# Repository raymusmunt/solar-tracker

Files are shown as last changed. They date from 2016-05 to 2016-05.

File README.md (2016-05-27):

# Solar Tracker
A solar tracking system using a barndoor mechanism with a Arduino microcontroller

**All 3D printable items can be found in the sketchup document**
- Brain Housing
- Motor housing hinge
- Captive bolt hinge
- Omron switch endstops
- LDR mount

Frame made with wood, attached to satellite mount with pole clamps.
Adjustable Solar Panel fixture made from aluminium cornering.

Worm gearing made with m10 threaded rod and nuts.
Motor Hinge and Captive bolt hinge also using threaded rod and bolts.

**Electronics**
- x2 LDR
- x2 Weatherproof microswitches
- x4 10K Resistors
- LM293B
- x4 Diodes (not needed if using LM293D)
- 12V DC Motor

Big thanks to all the folks at #Arduino for the help and encouragement!

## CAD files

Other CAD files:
assembly/solar_tracker_sketchup.skp

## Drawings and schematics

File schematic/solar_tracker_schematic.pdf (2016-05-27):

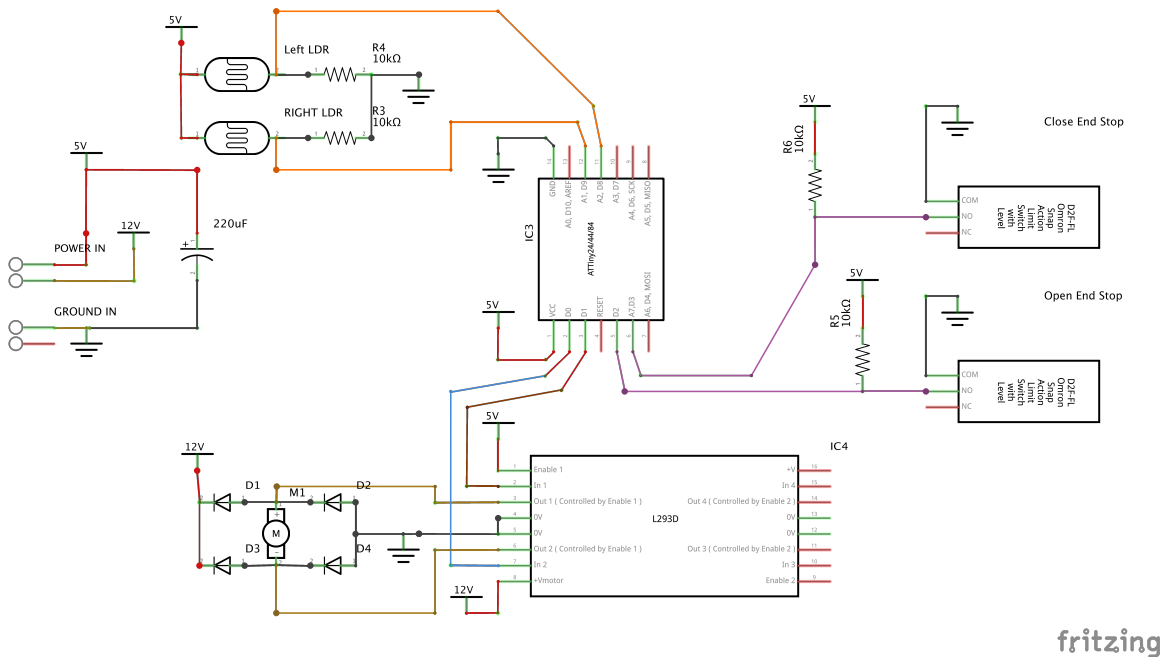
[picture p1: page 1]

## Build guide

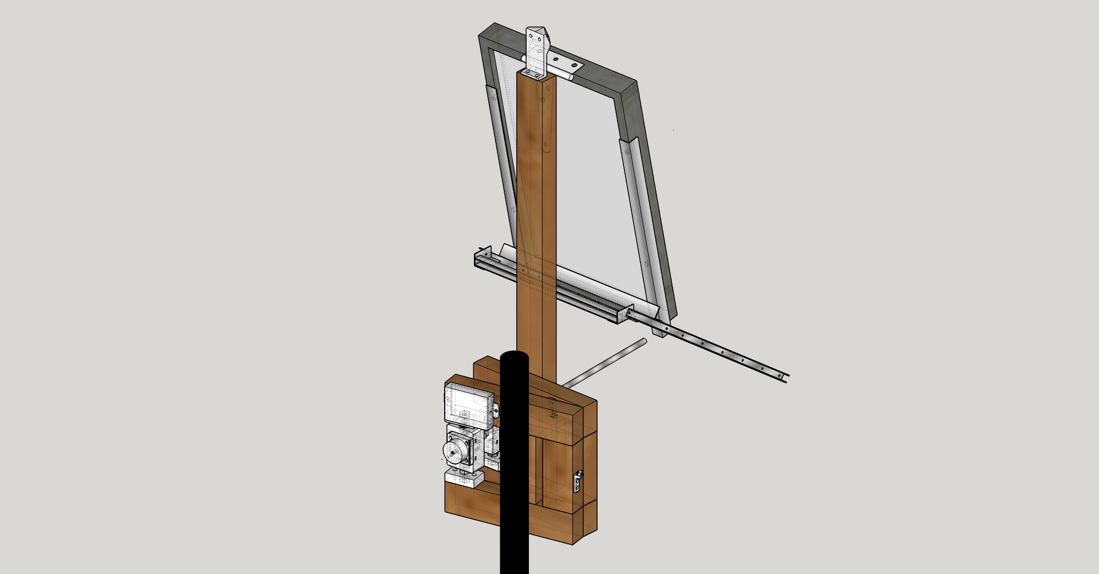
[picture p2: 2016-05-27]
assembly/solar_tracker_sketchup_back.jpg

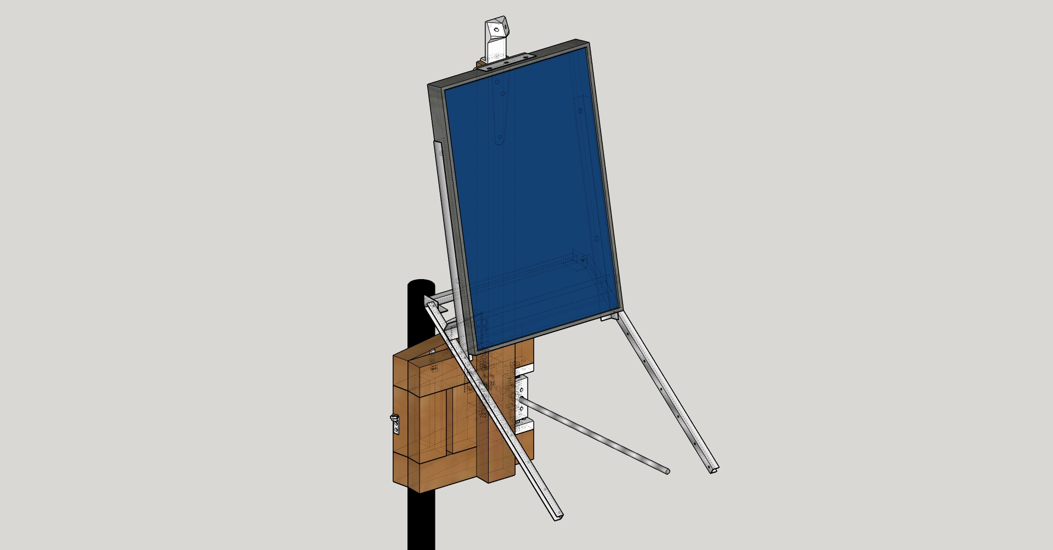
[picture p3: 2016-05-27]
assembly/solar_tracker_sketchup_front.jpg

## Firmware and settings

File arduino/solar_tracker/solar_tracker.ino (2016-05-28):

// ATMEL ATTINY84 / ARDUINO
//
//                           +-\/-+
//                     VCC  1|    |14  GND
//             (D 10)  PB0  2|    |13  AREF (D  0)
//             (D  9)  PB1  3|    |12  PA1  (D  1)
//                     PB3  4|    |11  PA2  (D  2)
//  PWM  INT0  (D  8)  PB2  5|    |10  PA3  (D  3)
//  PWM        (D  7)  PA7  6|    |9   PA4  (D  4)
//  PWM        (D  6)  PA6  7|    |8   PA5  (D  5)        PWM
//                           +----+

//////////////////
// SERIAL DEBUG //
//////////////////

// uncomment '#define DEBUG' to enable serial debug
//#define DEBUG

#ifdef DEBUG
  #include <SoftwareSerial.h>
  SoftwareSerial mySerial(4, 5);
  
  #define DEBUG_BEGIN(x) mySerial.begin(x)
  #define DEBUG_PRINT(x)     mySerial.print (x)
  #define DEBUG_PRINTLN(x)  mySerial.println (x)
  #define DEBUG_DELAY(x) delay(x)
  #else
  #define DEBUG_BEGIN(x)
  #define DEBUG_PRINT(x)
  #define DEBUG_PRINTLN(x)
  #define DEBUG_DELAY(x)
#endif

////////////////////
// WATCHDOG RESET //
////////////////////

#include <avr/sleep.h>
#include <avr/wdt.h>

ISR(WDT_vect)
{
  wdt_disable();  // disable watchdog
}

//////////////////////
// GLOBAL VARIABLES //
//////////////////////

#define LDR_LEFT A2
#define LDR_RIGHT A1

#define MOTOR_OPEN 10
#define MOTOR_CLOSE 9

#define SWITCH_OPEN 8
#define SWITCH_CLOSE 7

#define LEFT_FUDGE 0.015 // LeftSensor adjustment e.g. '0.11' adds 11%
#define TOTAL_FUDGE 2 // Add some slop to the motor centered figure.

#define NIGHT_VALUE 720

#define SLEEP_TIME 15 // 15 = 2min (8s * 15)

enum State {
  MAIN,
  GO_HOME,
  TRACK,
  SLEEP
};

State currentState = MAIN;

int ldrLeft, ldrRight;

////////////
// SETUP  //
////////////

void setup() {

  DEBUG_BEGIN(9600);

  pinMode(LDR_LEFT, INPUT);
  pinMode(LDR_RIGHT, INPUT);

  pinMode(MOTOR_OPEN, OUTPUT);
  pinMode(MOTOR_CLOSE, OUTPUT);

  pinMode(SWITCH_OPEN, INPUT);
  pinMode(SWITCH_CLOSE, INPUT);
}

///////////////
// MAIN LOOP //
///////////////

void loop() {

  DEBUG_DELAY(1000);

  switch ( currentState ) {

    /**
       [MAIN]
        Determines which state to enter based on ambient light
    */
    case MAIN:
      DEBUG_PRINTLN("State: MAIN");

      if ( isDaytime() ) {
        currentState = TRACK;
      } else if ( !isDaytime() ) {
        currentState = GO_HOME;
      }
      break;

    /**
       [TRACK]
        Looks for the sun and controls the motor allowing TOTAL_FUDGE slack
        in readings. Stops motor on contact with corresponding end stop.
    */
    case TRACK:
      DEBUG_PRINTLN("State: TRACK");

      readLDRs();

      if (ldrRight >= ldrLeft - TOTAL_FUDGE && ldrRight <= ldrLeft + TOTAL_FUDGE) {
        DEBUG_PRINTLN("Sweet Spot");
        stopMotor();
        currentState = MAIN;
        break;
      }
      
      if ( ldrRight > ldrLeft) {
        if ( !digitalRead(SWITCH_OPEN) ) {
          DEBUG_PRINTLN("Open End Stop");
          stopMotor();
          currentState = MAIN;
          break;
        }
        goRight();
      }
      
      else if ( ldrRight < ldrLeft ) {
        if ( !digitalRead(SWITCH_CLOSE) ) {
          DEBUG_PRINTLN("Closed End Stop");
          stopMotor();
          currentState = MAIN;
          break;
        }
        goLeft();
      }

      currentState = MAIN;
      break;

    /**
       [GO_HOME]
        Returns the panel to western configuration until
        it hits the end stop and goes to sleep.
    */
    case GO_HOME:
      DEBUG_PRINTLN("State: GO_HOME");
      if (!digitalRead(SWITCH_CLOSE)) {
        stopMotor();
        currentState = SLEEP;
        break;
      }
      goLeft();
      currentState = MAIN;
      break;

    /**
       [SLEEP]
        Power down for 8 seconds * SLEEP_TIME.
        http://forum.arduino.cc/index.php?topic=173850.msg1291338#msg1291338
    */
    case SLEEP:
      DEBUG_PRINTLN("State: SLEEP");

      for ( int i = 0; i < SLEEP_TIME; i++ ) {
        MCUSR = 0;                          // reset various flags
        WDTCSR |= 0b00011000;               // see docs, set WDCE, WDE
        WDTCSR =  0b01000000 | 0b100001;    // set WDIE, and 8s delay

        wdt_reset();
        set_sleep_mode (SLEEP_MODE_PWR_DOWN);
        sleep_mode();            // now goes to Sleep and waits for the interrupt
      }

      DEBUG_PRINTLN("Waking!");
      currentState = MAIN;
      break;

    default:
      DEBUG_PRINTLN("CODE FAILURE");
      stopMotor();
      currentState = MAIN;
      break;
  }
}

///////////////
// UTILITIES //
///////////////

void readLDRs () {
  ldrLeft = analogRead(LDR_LEFT);
  ldrRight = analogRead(LDR_RIGHT);

  DEBUG_PRINT("LDR L : ");
  DEBUG_PRINT(ldrLeft);

  float ldrLeftFudge = ldrLeft * LEFT_FUDGE;  // Calculate LEFT_FUDGE%
  ldrLeft = ldrLeft + (int)ldrLeftFudge;

  DEBUG_PRINT(" LDR L FUDGED : ");
  DEBUG_PRINT(ldrLeft);
  DEBUG_PRINT(" FUDGEVAL: ");
  DEBUG_PRINT(ldrLeftFudge);
  DEBUG_PRINT(" LDR R: ");
  DEBUG_PRINTLN(ldrRight);
}

bool isDaytime()
{
  readLDRs();

  if ( ldrLeft > NIGHT_VALUE || ldrRight > NIGHT_VALUE ) {
    return true;
  }
  return false;
}

////////////////////
// MOTOR CONTROLS //
////////////////////

void goRight()
{
  DEBUG_PRINTLN("Going Right");
  digitalWrite(MOTOR_OPEN, HIGH);
  digitalWrite(MOTOR_CLOSE, LOW);
}

void goLeft()
{
  DEBUG_PRINTLN("Going Left");
  digitalWrite(MOTOR_OPEN, LOW);
  digitalWrite(MOTOR_CLOSE, HIGH);
}

void stopMotor()
{
  DEBUG_PRINTLN("Stopping");
  digitalWrite(MOTOR_OPEN, LOW);
  digitalWrite(MOTOR_CLOSE, LOW);
}

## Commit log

2016-05-27 First Commit
    This appears to be working :) Any questions feel free to ask.
    [solar_tracker_fritzing.fzz, solar_tracker_sketchup.skp]
2016-05-27 Always something
    tweak while up ladder in the sun :D More decoupling required and LDR
    values changed when mounted wall.
2016-05-27 Cleaned up a bit
    comments corrected and serial prints trimmed down.
    [solar_tracker.ino]
2016-05-27 Siliconed and hot glued ...
    I reckon it’d probably work better with less fudge.
2016-05-28 This will do ...
    Go with this until i rebuild the hardware. LDR’s giving funny values
    at night time.
